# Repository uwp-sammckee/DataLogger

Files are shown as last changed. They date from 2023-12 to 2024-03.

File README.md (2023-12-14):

# DataLogger

PACKET BREAKDOWN:
0-roll\
1-pitch\
2-yaw\
3-alitude\
4-pressure\
5-temperature\
6-accX\
7-accY\
8-accZ\
9-gyroX\
10-gyroY\
11-gyroZ\
12-time\
13-placeholder\
14-placeholder\
15-placeholder

## Record.py
You need python, and the pyserial package\
`pip install pyserial`

Usage `python record.py <device>`\
ex. `python record.py com3`

## Coding Conventions
### Naming Conventions
  -Constants should be capitalized and in snake case\
  -Variables should be in camel case\
  -Functions/methods should be in snake case\
  -Classes should be in camel case\

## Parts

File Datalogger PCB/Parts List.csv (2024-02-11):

Index | Manufacturer Part Number | Manufacturer Name | Description | Availability | Stock Status | Attrition % | Requested Quantity 1 | Pack Quantity 1 | Pack Type 1 | Digi-Key Part Number 1 | Unit Price 1 | Extended Price 1 | Minimum Order Quantity 1
1 | CMT-9648-85T | CUI Devices | BUZZER MAGNETIC 5V 9MM TH | 3,318 | In Stock |  | 1 | 1 | Box | 102-CMT-9648-85T-ND | 0.70000 | $0.70 | 1
2 | CL10B104KB8NNWC | Samsung Electro-Mechanics | CAP CER 0.1UF 50V X7R 0603 | 6,657,112 | In Stock |  | 2 | 2 | Cut Tape (CT) | 1276-1935-1-ND | 0.10000 | $0.20 | 1
3 | GCM188R71E124KA37D | Murata Electronics | CAP CER 0.12UF 25V X7R 0603 | 2,575 | In Stock |  | 1 | 1 | Cut Tape (CT) | 490-GCM188R71E124KA37DCT-ND | 0.12000 | $0.12 | 1
4 | CL10A105KA8NNNC | Samsung Electro-Mechanics | CAP CER 1UF 25V X5R 0603 | 2,485,264 | In Stock |  | 1 | 1 | Cut Tape (CT) | 1276-1102-1-ND | 0.10000 | $0.10 | 1
5 | CL10A106MQ8NNNC | Samsung Electro-Mechanics | CAP CER 10UF 6.3V X5R 0603 | 1,552,558 | In Stock |  | 1 | 1 | Cut Tape (CT) | 1276-1119-1-ND | 0.11000 | $0.11 | 1
6 | CL10A226MP8NUNE | Samsung Electro-Mechanics | CAP CER 22UF 10V X5R 0603 | 1,770,047 | In Stock |  | 1 | 1 | Cut Tape (CT) | 1276-1274-1-ND | 0.18000 | $0.18 | 1
7 | B38G3RGB-20D0010H2U1930 | Harvatek Corporation | LED RGB DIFFUSED 0606 SMD | 1,861 | In Stock |  | 1 | 1 | Cut Tape (CT) | 3147-B38G3RGB-20D0010H2U1930CT-ND | 0.21000 | $0.21 | 1
8 | TS02-66-70-BK-160-LCR-D | CUI Devices | 6 X 6 MM, 7 MM ACTUATOR HEIGHT, | 18,948 | In Stock |  | 1 | 1 | Bag | 2223-TS02-66-70-BK-160-LCR-D-ND | 0.10000 | $0.10 | 1
9 | HPH2-A-04-UA | Adam Tech | CONN HEADER VERT 4POS 1.27MM | 1,679 | In Stock |  | 1 | 1 | Bag | 2057-HPH2-A-04-UA-ND | 0.18000 | $0.18 | 1
10 | G800W305018EU | Amphenol ICC (Commercial Products) | PIN HEADER 2.54MM PITCH STR,1X3P | 18,582 | In Stock |  | 4 | 4 | Bag | 664-G800W305018EU-ND | 0.10000 | $0.40 | 1
11 | M50-3530442 | Harwin Inc. | CONN HEADER VERT 4POS 1.27MM | 13,595 | In Stock |  | 2 | 2 | Box | 952-3600-ND | 0.21000 | $0.42 | 1
12 | EB147A-04-D | Adam Tech | EURO BLOCK, 4 POSITION | 1,255 | In Stock |  | 2 | 2 | Box | 2057-EB147A-04-D-ND | 1.19000 | $2.38 | 1
13 | EB147A-02-D | Adam Tech | EURO BLOCK, 2 POSITION | 3,880 | In Stock |  | 1 | 1 | Box | 2057-EB147A-02-D-ND | 0.78000 | $0.78 | 1
14 | RMCF0603FT100R | Stackpole Electronics Inc | RES 100 OHM 1% 1/10W 0603 | 1,691,589 | In Stock |  | 4 | 4 | Cut Tape (CT) | RMCF0603FT100RCT-ND | 0.10000 | $0.40 | 1
15 | RMCF0603FT5K10 | Stackpole Electronics Inc | RES 5.1K OHM 1% 1/10W 0603 | 1,137,263 | In Stock |  | 4 | 4 | Cut Tape (CT) | RMCF0603FT5K10CT-ND | 0.10000 | $0.40 | 1
16 | RMCF0603FT10K0 | Stackpole Electronics Inc | RES 10K OHM 1% 1/10W 0603 | 11,474,360 | In Stock |  | 4 | 4 | Cut Tape (CT) | RMCF0603FT10K0CT-ND | 0.10000 | $0.40 | 1
17 | RMCF0603FT4K02 | Stackpole Electronics Inc | RES 4.02K OHM 1% 1/10W 0603 | 67,438 | In Stock |  | 1 | 1 | Cut Tape (CT) | RMCF0603FT4K02CT-ND | 0.10000 | $0.10 | 1
18 | HPH2-A-08-UA | Adam Tech | CONN HEADER VERT 8POS 1.27MM | 3,032 | In Stock |  | 1 | 1 | Bag | 2057-HPH2-A-08-UA-ND | 0.36000 | $0.36 | 1
19 | DEV-20359 | SparkFun Electronics | TEENSY 4.1 WITHOUT ETHERNET | 947 | In Stock |  | 1 | 1 | Bulk | 1568-DEV-20359-ND | 31.08000 | $31.08 | 1
20 | BNO055 | Bosch Sensortec | IMU ACCEL/GYRO/MAG I2C 28LGA | 13,291 | In Stock |  | 1 | 1 | Cut Tape (CT) | 828-1058-1-ND | 12.32000 | $12.32 | 1
21 | LPS25HBTR | STMicroelectronics | SENSOR 18.27PSIA 24BIT 10LLGA | 10,694 | In Stock |  | 1 | 1 | Cut Tape (CT) | 497-15070-1-ND | 6.37000 | $6.37 | 1
22 | AZ1117CH2-5.0TRG1 | Diodes Incorporated | IC REG LINEAR 5V 1A SOT223 | 19,907 | In Stock |  | 1 | 1 | Cut Tape (CT) | 31-AZ1117CH2-5.0TRG1CT-ND | 0.35000 | $0.35 | 1
23 | W25Q128JVSIQ TR | Winbond Electronics | IC FLASH 128MBIT SPI/QUAD 8SOIC | 333,238 | In Stock |  | 1 | 1 | Cut Tape (CT) | W25Q128JVSIQCT-ND | 1.72000 | $1.72 | 1
24 | VN5E160STR-E | STMicroelectronics | IC PWR SWITCH N-CHANNEL 1:1 8SO | 25,523 | In Stock |  | 4 | 4 | Cut Tape (CT) | 497-18886-1-ND | 1.83000 | $7.32 | 1

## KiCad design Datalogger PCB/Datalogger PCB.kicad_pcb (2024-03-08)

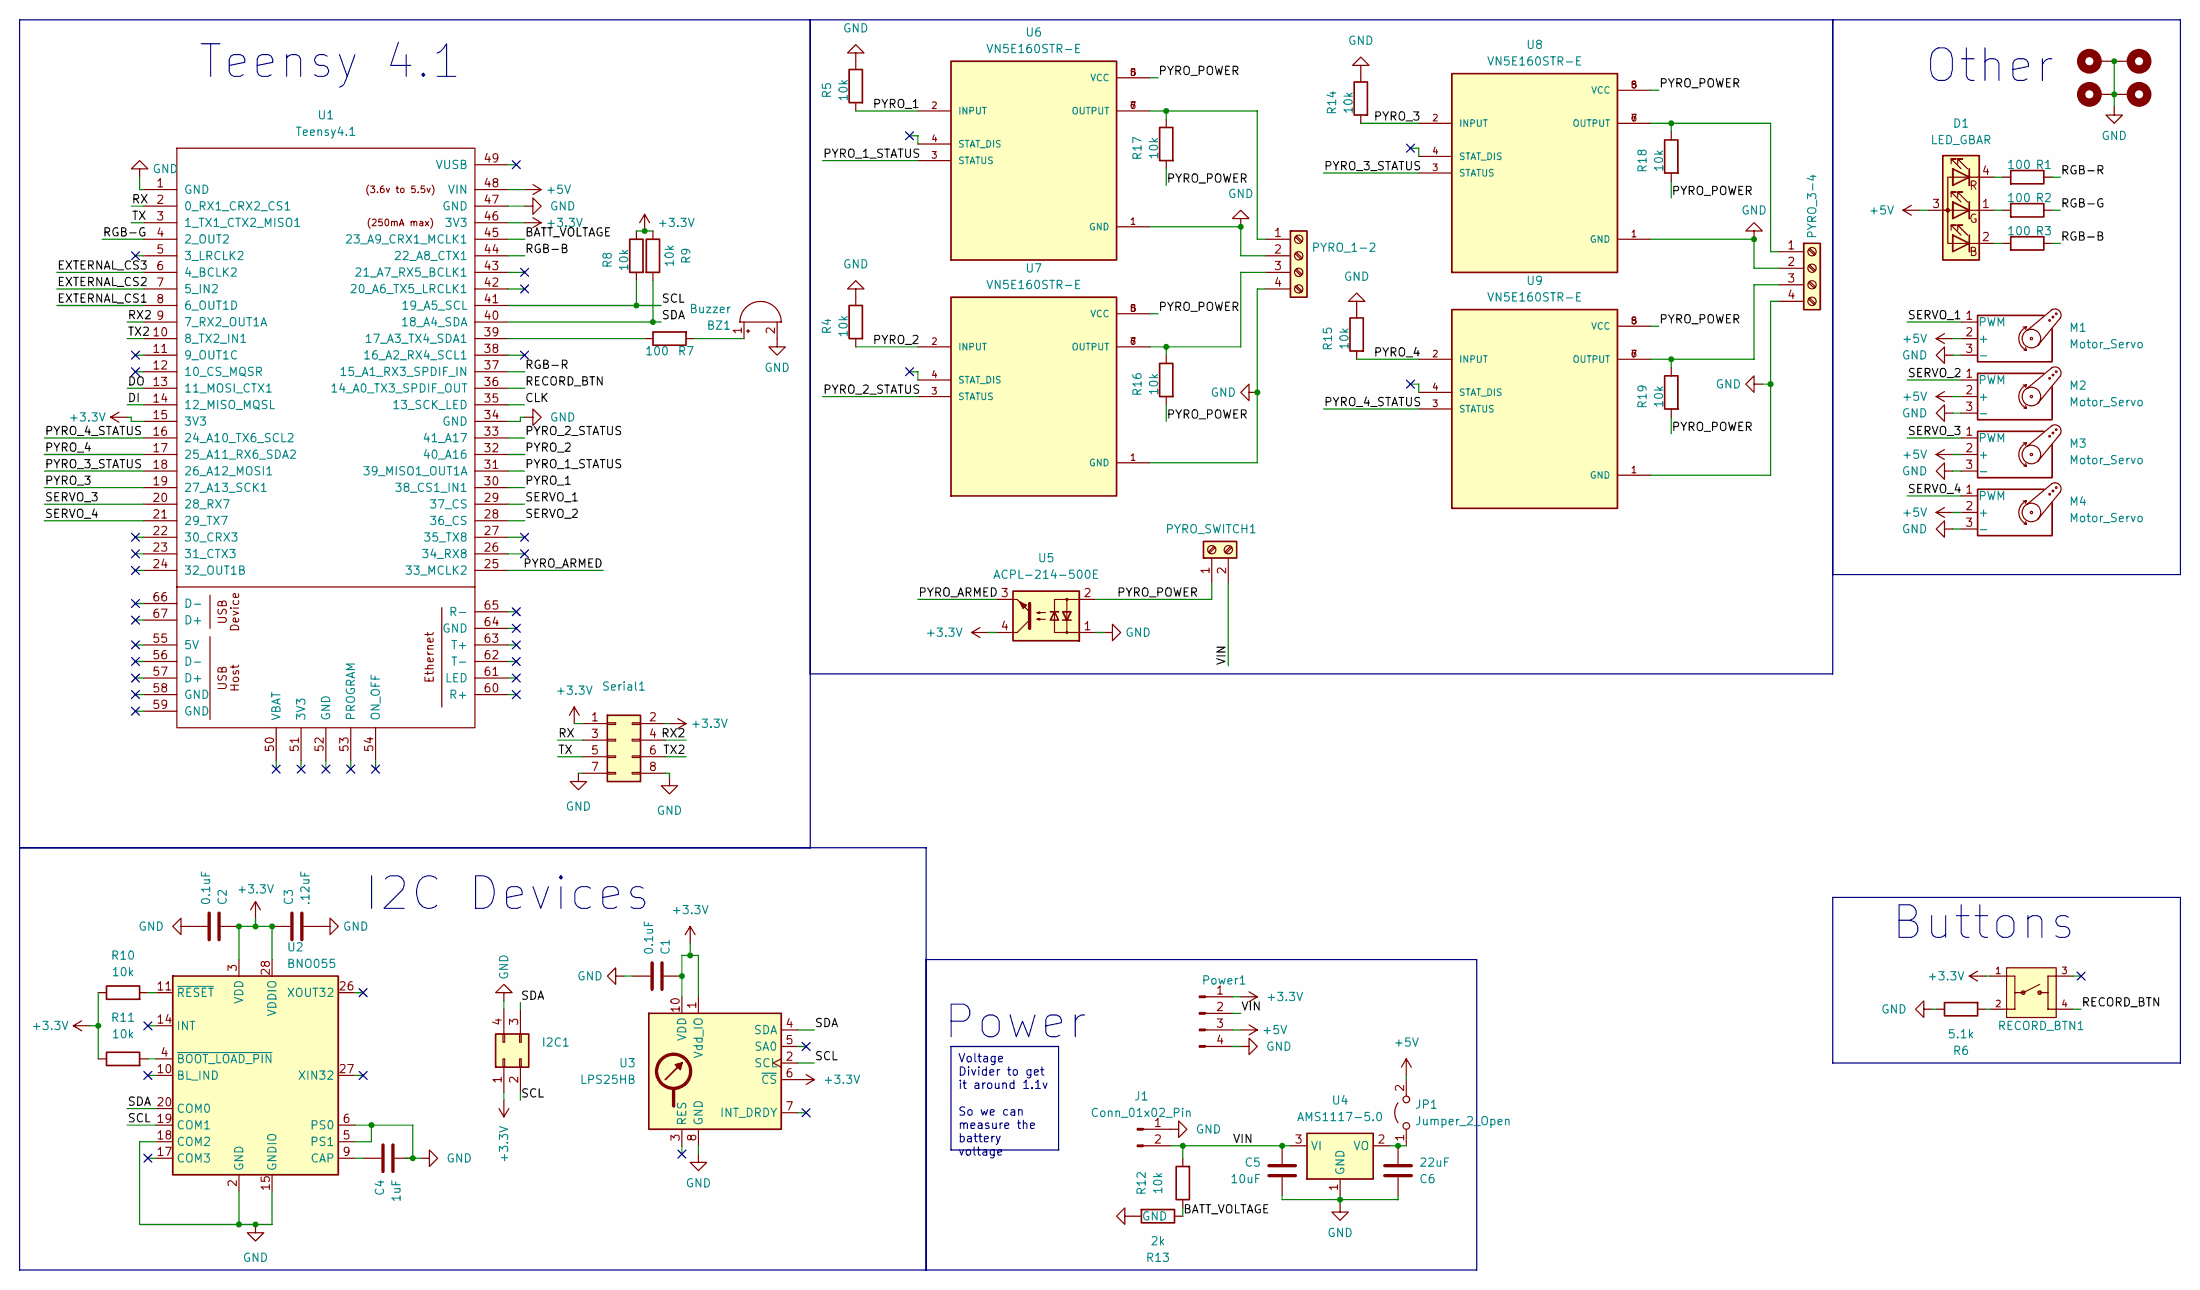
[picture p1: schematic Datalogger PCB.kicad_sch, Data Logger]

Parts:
BZ1: Buzzer; Buzzer_12x9.5RM7.6
C1, C2: 0.1uF; R_0603_1608Metric_Pad0.98x0.95mm_HandSolder
C3: .12uF; R_0603_1608Metric_Pad0.98x0.95mm_HandSolder
C4: 1uF; R_0603_1608Metric_Pad0.98x0.95mm_HandSolder
C5: 10uF; R_0603_1608Metric_Pad0.98x0.95mm_HandSolder
C6: 22uF; R_0603_1608Metric_Pad0.98x0.95mm_HandSolder
D1: LED_GBAR
H1, H2, H3, H4: MountingHole_Pad; MountingHole_3.2mm_M3_Pad_TopBottom
I2C1: Conn_02x02_Counter_Clockwise; PinHeader_2x02_P2.54mm_Vertical
J1: Conn_01x02_Pin; PinHeader_1x02_P2.54mm_Vertical
JP1: Jumper_2_Open; PinHeader_1x02_P2.54mm_Vertical
M1, M2, M3, M4: Motor_Servo; PinHeader_1x03_P2.54mm_Vertical
PYRO_1-2, PYRO_3-4: Screw_Terminal_01x04; TerminalBlock_bornier-4_P5.08mm
PYRO_SWITCH1: Screw_Terminal_01x02; TerminalBlock_bornier-2_P5.08mm
Power1: Conn_01x04_Pin; PinHeader_1x04_P2.54mm_Vertical
R1, R2, R3, R7: 100; R_0603_1608Metric_Pad0.98x0.95mm_HandSolder
R4, R5, R8, R9, R10, R11, R12, R14, R15, R16, R17, R18, R19: 10k; R_0603_1608Metric_Pad0.98x0.95mm_HandSolder
R6: 5.1k; R_0603_1608Metric_Pad0.98x0.95mm_HandSolder
R13: 2k; R_0603_1608Metric_Pad0.98x0.95mm_HandSolder
RECORD_BTN1: FSM8JH; SW_FSM8JH; PARTREV C10
Serial1: Conn_02x04_Odd_Even; PinHeader_2x04_P2.54mm_Vertical
U1: Teensy4.1; Teensy41
U2: BNO055; LGA-28_5.2x3.8mm_P0.5mm
U3: LPS25HB; ST_HLGA-10_2.5x2.5mm_P0.6mm_LayoutBorder3x2y
U4: AMS1117-5.0; SOT-223-3_TabPin2
U5: ACPL-214-500E; SOP-4_4.4x2.6mm_P1.27mm
U6, U7, U8, U9: VN5E160STR-E; SOIC127P600X175-8N; PARTREV 3

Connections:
+3.3V: C1.1, C2.1, C3.1, I2C1.1, Power1.1, R8.1, R9.1, R10.1, R11.1, RECORD_BTN1.1, Serial1.1, Serial1.2, U1.15 (3V3), U1.46 (3V3), U2.3 (VDD), U2.28 (VDDIO), U3.1 (Vdd_IO), U3.6 (~CS), U3.10 (VDD), U5.4
+5V: D1.3 (A), JP1.2 (B), M1.2 (+), M2.2 (+), M3.2 (+), M4.2 (+), Power1.3, U1.48 (VIN)
/BATT_VOLTAGE: R12.1, R13.1, U1.45 (23_A9_CRX1_MCLK1)
/CLK: U1.35 (13_SCK_LED)
/DI: U1.14 (12_MISO_MQSL)
/DO: U1.13 (11_MOSI_CTX1)
/EXTERNAL_CS1: U1.8 (6_OUT1D)
/EXTERNAL_CS2: U1.7 (5_IN2)
/EXTERNAL_CS3: U1.6 (4_BCLK2)
/PYRO_1: R5.2, U1.30 (38_CS1_IN1), U6.2 (INPUT)
/PYRO_1_STATUS: U1.31 (39_MISO1_OUT1A), U6.3 (STATUS)
/PYRO_2: R4.2, U1.32 (40_A16), U7.2 (INPUT)
/PYRO_2_STATUS: U1.33 (41_A17), U7.3 (STATUS)
/PYRO_3: R14.2, U1.19 (27_A13_SCK1), U8.2 (INPUT)
/PYRO_3_STATUS: U1.18 (26_A12_MOSI1), U8.3 (STATUS)
/PYRO_4: R15.2, U1.17 (25_A11_RX6_SDA2), U9.2 (INPUT)
/PYRO_4_STATUS: U1.16 (24_A10_TX6_SCL2), U9.3 (STATUS)
/PYRO_ARMED: U1.25 (33_MCLK2), U5.3
/PYRO_POWER: PYRO_SWITCH1.1, R16.2, R17.2, R18.2, R19.2, U5.2, U6.5 (VCC), U6.8 (VCC), U7.5 (VCC), U7.8 (VCC), U8.5 (VCC), U8.8 (VCC), U9.5 (VCC), U9.8 (VCC)
/RECORD_BTN: RECORD_BTN1.4, U1.36 (14_A0_TX3_SPDIF_OUT)
/RGB-B: R3.1, U1.44 (22_A8_CTX1)
/RGB-G: R2.1, U1.4 (2_OUT2)
/RGB-R: R1.1, U1.37 (15_A1_RX3_SPDIF_IN)
/RX: Serial1.3, U1.2 (0_RX1_CRX2_CS1)
/RX2: Serial1.4, U1.9 (7_RX2_OUT1A)
/SCL: I2C1.2, R8.2, U1.41 (19_A5_SCL), U2.19 (COM1), U3.2 (SCL)
/SDA: I2C1.3, R9.2, U1.40 (18_A4_SDA), U2.20 (COM0), U3.4 (SDA)
/SERVO_1: M1.1 (PWM), U1.29 (37_CS)
/SERVO_2: M2.1 (PWM), U1.28 (36_CS)
/SERVO_3: M3.1 (PWM), U1.20 (28_RX7)
/SERVO_4: M4.1 (PWM), U1.21 (29_TX7)
/TX: Serial1.5, U1.3 (1_TX1_CTX2_MISO1)
/TX2: Serial1.6, U1.10 (8_TX2_IN1)
/VIN: C5.1, J1.2, PYRO_SWITCH1.2, Power1.2, R12.2, U4.3 (VI)
GND: BZ1.2 (+), C1.2, C2.2, C3.2, C4.2, C5.2, C6.1, H1.1, H2.1, H3.1, H4.1, I2C1.4, J1.1, M1.3 (-), M2.3 (-), M3.3 (-), M4.3 (-), PYRO_1-2.2, PYRO_1-2.4, PYRO_3-4.2, PYRO_3-4.4, Power1.4, R4.1, R5.1, R6.1, R13.2, R14.1, R15.1, Serial1.7, Serial1.8, U1.1 (GND), U1.34 (GND), U1.47 (GND), U2.2 (GND), U2.5 (PS1), U2.6 (PS0), U2.15 (GNDIO), U2.16 (GNDIO), U2.18 (COM2), U2.25 (GNDIO), U3.8 (GND), U3.9 (GND), U4.1 (GND), U5.1, U6.1 (GND), U7.1 (GND), U8.1 (GND), U9.1 (GND)
unnamed: BZ1.1 (-), R7.2
unnamed: D1.2 (BK), R3.2
unnamed: D1.1 (GK), R2.2
unnamed: D1.4 (RK), R1.2
unnamed: C6.2, JP1.1 (A), U4.2 (VO)
unnamed: PYRO_1-2.1, R17.1, U6.6 (OUTPUT), U6.7 (OUTPUT)
unnamed: PYRO_1-2.3, R16.1, U7.6 (OUTPUT), U7.7 (OUTPUT)
unnamed: PYRO_3-4.1, R18.1, U8.6 (OUTPUT), U8.7 (OUTPUT)
unnamed: PYRO_3-4.3, R19.1, U9.6 (OUTPUT), U9.7 (OUTPUT)
unnamed: R6.2, RECORD_BTN1.2
unnamed: R7.1, U1.39 (17_A3_TX4_SDA1)
unnamed: C4.1, U2.9 (CAP)
unnamed: R11.2, U2.4 (~BOOT_LOAD_PIN)
unnamed: R10.2, U2.11 (~RESET)

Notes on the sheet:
Voltage Divider to get it around 1.1v So we can measure the battery voltage
Other
Teensy 4.1
Buttons
Power
I2C Devices

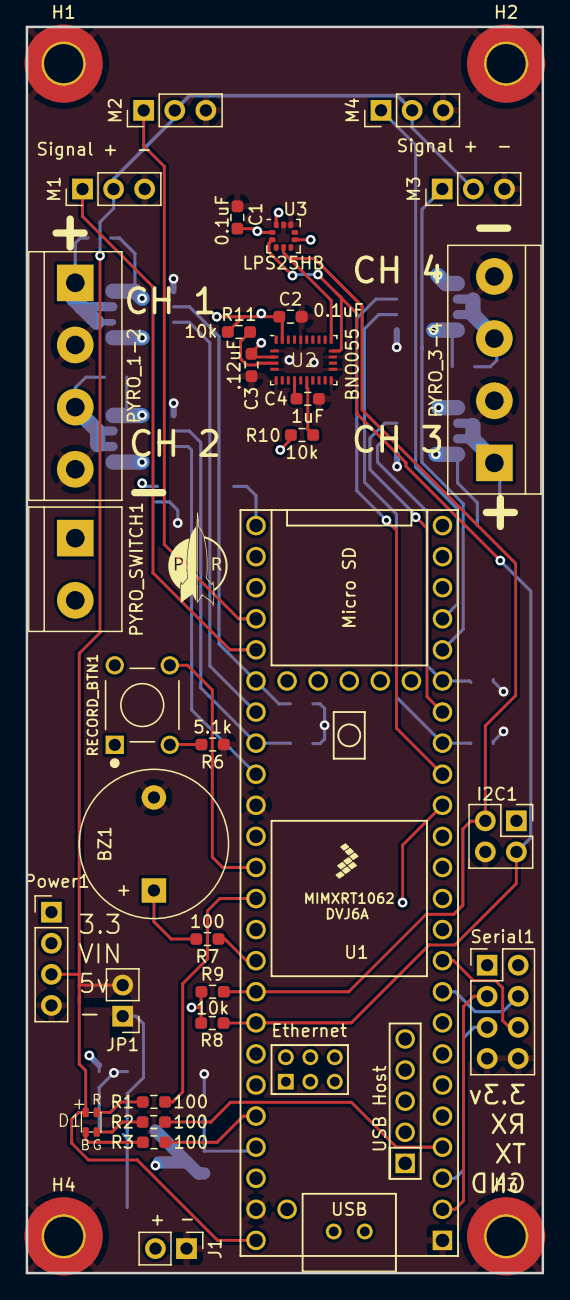
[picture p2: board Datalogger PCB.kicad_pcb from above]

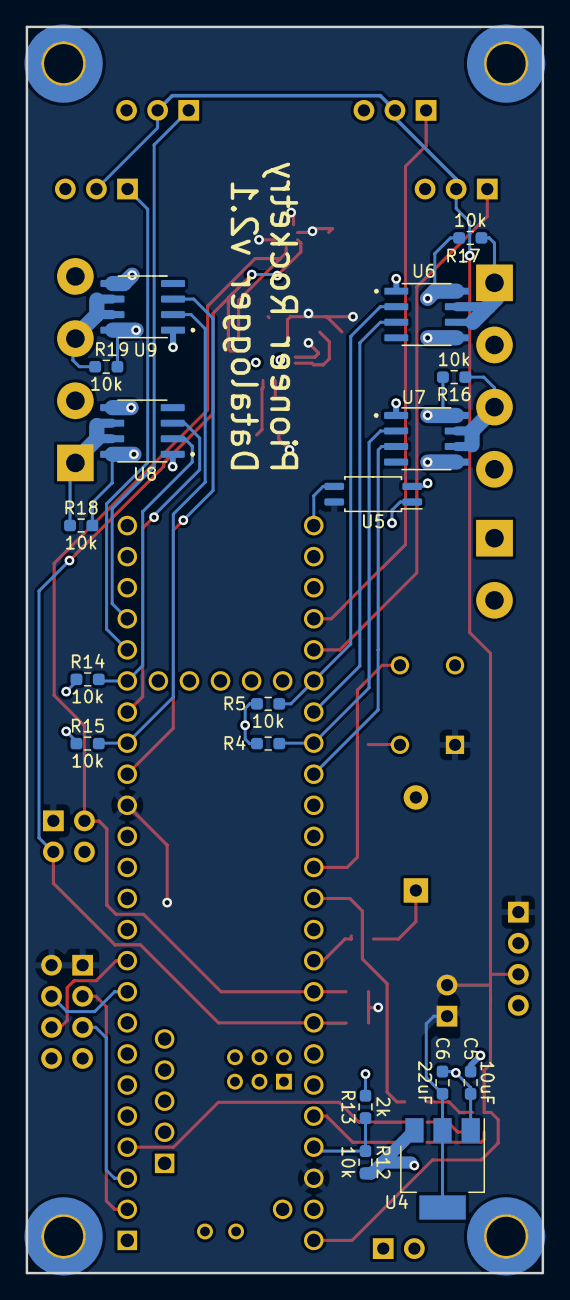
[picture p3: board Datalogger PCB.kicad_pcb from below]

Board: 4 copper layers, 42.2 x 101.8 mm, 53 parts (18 on the bottom side), 43 nets.

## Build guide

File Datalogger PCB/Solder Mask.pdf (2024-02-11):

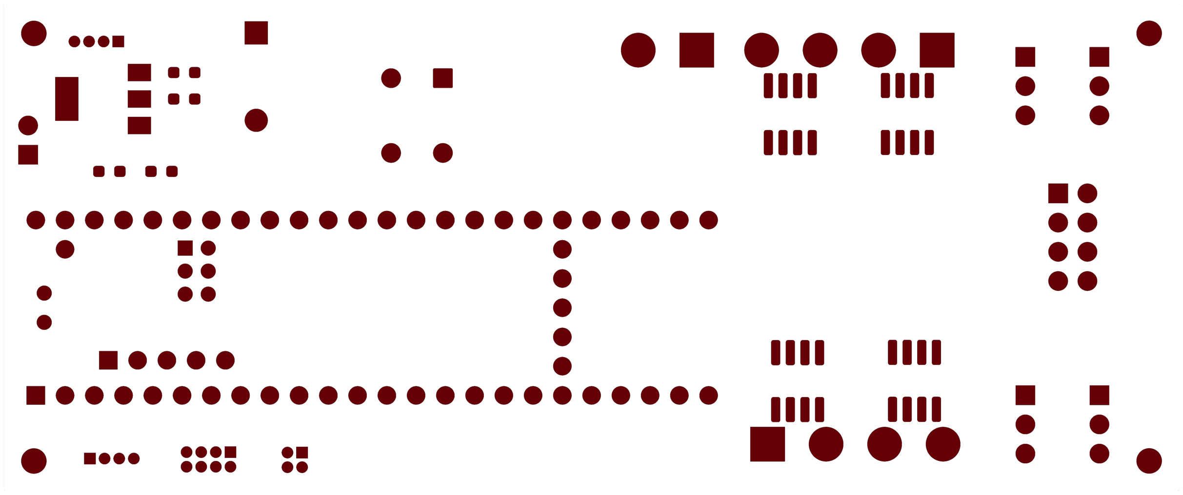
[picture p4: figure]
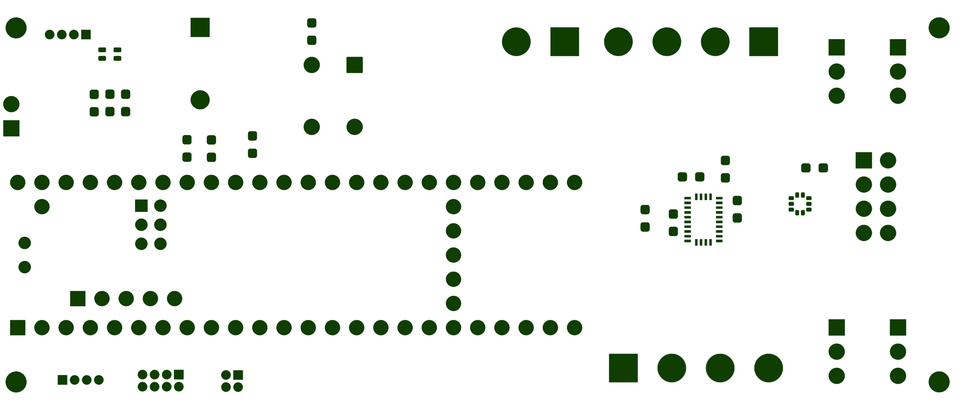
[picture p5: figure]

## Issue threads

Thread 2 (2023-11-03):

Reformat code to be more OOP

uwp-sammckee, 2023-11-03:

uwp-sammckee, 2023-11-06:
Made Memory, Buzzer, and ColorLED classes. Still need to create classes for each breakout board: gyro and altimeter.

Closed 2023-11-19.

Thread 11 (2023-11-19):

New PCB layout

uwp-sammckee, 2023-11-19:

PizzaRules668, 2023-11-19:
Here is what I am think about for parts

- [Processor](https://www.pjrc.com/store/teensy41.html)
- [LPS25HBTR](https://www.digikey.com/en/products/detail/stmicroelectronics/LPS25HBTR/5043059)
- [BNO055](https://www.digikey.com/en/products/detail/bosch-sensortec/BNO055/6136301)
- Same Flash chip [W25Q128](https://www.digikey.com/en/products/detail/winbond-electronics/W25Q128JVSIQ-TR/

PizzaRules668, 2023-12-04:
I **think** the latest revision is done
It has 4 Pyro Channels, A Pyro channel Switch, 4 Servo Mounts, 2 buttons (record, dump, [I think I could get rid of them if we want]).

uwp-sammckee, 2023-12-05:
What's your plan for getting rid of the record and dump buttons?

uwp-sammckee, 2023-12-05:
Is there a LED for state indication on the new design?

uwp-sammckee, 2023-12-05:
The board looks good otherwise! I have a couple of questions about what some of the pin outs do, but we can discuss that on Tuesday.

PizzaRules668, 2023-12-05:
I was thinking we could get rid of the dump button, and we could do the same thing with the erase button where it can only be done by user input.
There is an LED it below the buzzer its an SMD buzzer.

PizzaRules668, 2023-12-06:
[Digikey Parts List](https://www.digikey.com/en/mylists/list/UNYX1KHIE8)

Closed 2024-02-11.

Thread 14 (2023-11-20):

Valid that sensor fusion on data logger

uwp-sammckee, 2023-11-20:

uwp-sammckee, 2023-11-20:
Make sure that the roll, pitch, and yaw is coming from the sensor fusion of the accelerometer and gyroscope. In addition, identify what filter is being used to sensor fuse the accelerometer or gyroscope (complementary or Kalman)

Closed 2024-01-27.

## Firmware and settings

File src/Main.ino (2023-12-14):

#include "Wire.h"
#include <MPU6050_light.h>

#include "ColorLED.h"
#include "Buzzer.h"
#include "Memory.h"
#include "Accelerometer.h"
#include "Barometer.h"
#include "State_Machine.h"

const int PIN_RECORD_DATA = 5;
const int PIN_DUMP_DATA = A2;
const int PIN_ERASE_DATA = A1;

const int PIN_SD_CARD_CS = 7;

const int MPU = 0x68; // MPU6050 I2C address

bool recordData = false;
int recordDataState = 0; 

bool dumpData = false;
int dumpDataState = 0; 

bool eraseData = false;
int eraseDataState = 0; 

MPU6050 mpu(Wire);

Buzzer buzzer;
ColorLED LED;
Accelerometer accelerometer(mpu);
Barometer baro;
Memory memory;

State_Machine state_machine(accelerometer);

const unsigned long LOOP_LENGTH = 50;
unsigned long loopDelay  = 0;
unsigned long loopStart  = 0;
unsigned long timeStart  = 0;

specialFloatT data[16];

void setup() {
  Serial.begin(19200);
  Serial.println(state_machine.get_state());
  Wire.begin();
  byte status = mpu.begin();
  Serial.println(status);
  while(status!=0){ } // stop everything if could not connect to MPU6050
  
  Serial.println(F("Calculating offsets, do not move MPU6050"));
  delay(1000);
  mpu.calcOffsets(true,true); // gyro and accelero
  
  pinMode(buzzer.get_buzzer_pin(), OUTPUT);

  pinMode(LED.get_red_pin(), OUTPUT);
  pinMode(LED.get_blue_pin(), OUTPUT);
  pinMode(LED.get_blue_pin(), OUTPUT); 

  pinMode(PIN_RECORD_DATA, INPUT);
  pinMode(PIN_DUMP_DATA, INPUT);
  pinMode(PIN_ERASE_DATA, INPUT);

  baro.begin(); // Get sensor online

  delay(20);
  buzzer.start_up_sound();
  Serial.println("Setup finished, everything is good.");
}

void loop() {
  loopStart = millis();
  LED.show_blue();
  //delay(100);

  recordDataState = digitalRead(PIN_RECORD_DATA);

  // // check if the pushbutton is pressed. If it is, the buttonState is HIGH:
  if (recordDataState == HIGH) {
    if (recordData) {
      recordData = false;
      delay(1000);
      Serial.println("recordData false");
    } else {
      timeStart = millis();
      recordData = true;
      delay(1000);
      Serial.println("recordData true");
    }
    Serial.println("recordData: "+String(recordData));
  }

  dumpDataState = digitalRead(PIN_DUMP_DATA);

  // // check if the pushbutton is pressed. If it is, the buttonState is HIGH:
  if (dumpDataState == HIGH) {
    if (dumpData) {
      dumpData = false;
      delay(1000);
    } else {
      dumpData = true;
      delay(1000);
    }
    delay(1000);
  }

  eraseDataState = digitalRead(PIN_ERASE_DATA);

  // // check if the pushbutton is pressed. If it is, the buttonState is HIGH:
  if (eraseDataState == HIGH) {
    if (eraseData) {
      eraseData = false;
      delay(1000);
    } else {
      eraseData = true;
      delay(1000);
    }
    delay(1000);
  }

    if (!recordData && !dumpData && !eraseData) {
    
    byte choice = Serial.read();

    if (choice == 'e') {
      memory.erase_data();
    }
  }

  if (recordData){
    LED.show_yellow();
    accelerometer.get_roll_pitch_yaw(data, mpu);
    // Serial.println("data getAngleX(): "+String(data[0].value));
    // Serial.print("/");
    // Serial.print(data[1].value);
    // Serial.print("/");
    // Serial.println(data[2].value);
    
    baro.get_alt_pres_temp(data);
    // Serial.print(data[3].value);
    // Serial.print("/");
    // Serial.print(data[4].value);
    // Serial.print("/");
    // Serial.println(data[5].value);

    data[12].value = (millis()-timeStart) / 1000.0f;

    data[13].value = (float)state_machine.check_state(data[6].value, data[3].value);

    // Serial.println();
    memory.write_data(data);
  }

  if (dumpData) {
    buzzer.start_sound();
    LED.show_red();
    memory.print_data_to_serial();
    buzzer.end_sound();
    dumpData = false;
  }
  
  loopDelay = LOOP_LENGTH - (millis() - loopStart);
  if (loopDelay > LOOP_LENGTH) loopDelay = 0;

  delay(loopDelay);
}

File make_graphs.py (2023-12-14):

import argparse



if __name__ == "__main__":
    args = parser.parse_args()

    device = args.device
    baud = args.baud

    conn = serial.Serial(port=device, baudrate=baud)

    if not os.path.exists("data/"):
        os.makedirs("data/")

    print("Serial Connection Open")
    i = 0
    while True:
        try:
            if conn.in_waiting:
                data = conn.readline().decode()

                print(data, end="")

                if "NAN,  NAN,  NAN,  NAN,  NAN,  NAN,  NAN,  NAN,  NAN,  NAN,  NAN,  NAN,  NAN,  NAN,  NAN,  NAN"  in data:
                    if i == 1:
                        break
                    else: i += 1

                if "DATA DONE" in data:
                    break
                    
                loggedData.append(data)

        except KeyboardInterrupt:
            print("Quiting")
            break

    
    print("Done Processing Data")
    processData()

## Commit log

2023-11-02 Should of been pushed to Feature-1
    [testCSV.CSV]
2023-11-02 Revert "Should of been pushed to Feature-1"
    This reverts commit 4001e513602efce9f8fc61a58f293b3ddfdde305.
    [testCSV.CSV]
2023-11-06 Made Memory, ColorLED, and Buzzer classes to increase organization, and renamed the main Arduino file.
    [Main.ino, Memory.cpp]
2023-11-12 Rename main file and add accelerometer class
2023-11-19 PCB-1 (#8)
    * Converted Breadboard to Schematic
    * Turn Schematic into PCB
    * Made board smaller (about 1.6x4inch)
    * Added Test
    * Added logo to PCB
    ---------
    [Datalogger PCB.kicad_pcb, Datalogger PCB.kicad_sch, FSM8JH.step]
2023-12-06 Fix memory loop, and fix record.py, as well as defined baudrate inside of the platformio.ini file
    [Main.ino, Memory.cpp, record.py]
2023-12-06 Fixed Const Loop Timing
    [Main.ino]
2023-12-14 7 feature (#18)
    * Preliminary state machine code, will need to redo bounds for each state
    * pull from main
    * Added and validated states machine logic, not bounds
    * moved README into base directory
    * Added some naming conventions to coding conventions in README
    * Corrected format of README
    * Corrected format of README
    * Added Velocity
    * funny commit
    * Funny commit 2
    * test launch 1 code
    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
    [Accelerometer.cpp, Main.ino, Memory.cpp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]
2024-02-11 V2 pcb (#19)
    Completed PCB design
    [Datalogger PCB.kicad_pcb, Datalogger PCB.kicad_sch, FSM8JH.step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]
2024-03-01 Made connectors bigger and removed unused radio connector
    [Datalogger PCB.kicad_pcb, Datalogger PCB.kicad_sch]
2024-03-03 Removed Diode and replaced with jumper
    [Datalogger PCB.kicad_pcb, Datalogger PCB.kicad_sch]
2024-03-03 Added pyro armed
    [Datalogger PCB.kicad_sch]
2024-03-03 Added continuity resistors
    [Datalogger PCB.kicad_pcb, Datalogger PCB.kicad_sch]
2024-03-03 Grounded Connector
    [Datalogger PCB.kicad_pcb, Datalogger PCB.kicad_sch]
2024-03-03 Made power jumper standard
    [Datalogger PCB.kicad_pcb, Datalogger PCB.kicad_sch]
2024-03-08 Modified PCB
    [Datalogger PCB.kicad_pcb]
